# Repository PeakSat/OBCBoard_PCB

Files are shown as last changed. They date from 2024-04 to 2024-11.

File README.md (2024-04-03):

# AcubeSat - On Board Computer PCB

This repository contains schematics and layout files for
the On-Board Computer's PCB.

**NOTE:** EVERYTHING CONTAINED HERE IS UNTESTED AND WORK-IN-PROGRESS.
USE AT YOUR OWN RISK!

# Requirements
You will need **KiCad version 6** to open the schematics.
Your KiCad installation should contain the standard footprint library
in order for the layout files to be displayed normally.

# Usage
Open the `.kicad_pro` file in KiCad and then:
* choose the `.kicad_sch` file to view the schematic
* choose the `.kicad_pcb` file to view the PCB's layout.

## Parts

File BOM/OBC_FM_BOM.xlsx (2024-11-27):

Id | Designator | Footprint | Quantity | Designation | Supplier and ref | Tolerance | Min Op Temp | Max Op Temp | PPM/C | Power Rating
1 | CMD_EN,RTCI,WEN,TP27,ADDR_EN,TP32,TP31,TP45,TP10,NWP,PWM,BUSY,TP33,NOUT,TP37,TP34,TP47,NRST,TP49,TP36,GND,TP26,TP29,TP44,EN,TP6,RTCO,TP35,TP52,TP30,PWM,TP56,TP55 | TestPoint_Pad_D1.0mm | 33 | TestPoint_Small | - | - | - | - | -
2 | TP22,TP12,TP3,TP53,TP54 | TestPoint_Pad_D1.0mm | 5 | 5015 | - | - | - | - | -
3 | FID6,FID5,FID4,FID2,FID3,FID1 | Fiducial_0.5mm_Mask1mm | 6 | Fiducial | - | - | - | - | -
4 | 3V3_PROT,J29,ADCS_VDD,ADCS_VDDIO | PinHeader_1x01_P1.00mm_Vertical | 4 | Conn_01x01_Pin | - | - | - | - | -
5 | H4,H1,H3,H2 | MountingHole_3.2mm_M3_DIN965_Pad | 4 | MountingHole_Pad | - | - | - | - | -
 | D1 | FHA1105P-TR (LED_0402) | 1 | FHA1105P-TR | https://eu.mouser.com/ProductDetail/Stanley-Electric/FHA1105P-TR?qs=byeeYqUIh0MAYVMdncV%252BvA%3D%3D
6 | R65 | R_0603_1608Metric | 1 | 300k | https://gr.mouser.com/ProductDetail/Panasonic/ERJ-3EKF3003V | 1% | -55 | 155 | 100 | 100mW
7 | R90,R102,R101,R56,R99,R52,R64,R91,R58,R62,R89,R100,R104,R60,R54,R92,R50,R98,R97,R103 | R_0603_1608Metric | 20 | 1k | https://gr.mouser.com/ProductDetail/Panasonic/ERJ-3RBD102V?qs=FhbYA5MVMOXq%2Fpwdysel%252Bw%3D%3D | 0.5% | -55 | 155 | 50 | 100mW
8 | R83,R79,R77,R74 | R_0603_1608Metric | 4 | 30K | https://gr.mouser.com/ProductDetail/Panasonic/ERJ-S03F3002V?qs=Zyl8A9hlmJqIHk%2F7tV8Mgw%3D%3D | 1% | -55 | 155 | 100 | 100mW
9 | R117,R119,R118,R120 | R_0603_1608Metric | 4 | 0.5 | https://gr.mouser.com/ProductDetail/Wurth-Elektronik/560050316011?qs=unwgFEO1A6vnuH3MgbtkpQ%3D%3D
10 | R37,R126,R38,R127,R12,R23,R26,R11 | R_0402_1005Metric | 8 | 100k | https://gr.mouser.com/ProductDetail/Panasonic/ERJ-2RKF1003X?qs=H7k1u0Mp9JQnXoBKdf15Qg%3D%3D | 1% | -55 | 155 | 100 | 100mW
 | R19 | R_0402_1005Metric | 1 | 330 | https://eu.mouser.com/ProductDetail/Panasonic/ERA-2ARB331X?qs=6%252Bc%252B2ke79U7iqIhHbNRZlw%3D%3D
11 | R130,R48,R47,R131,R14,R15 | R_0402_1005Metric | 10 | 1.5k | https://gr.mouser.com/ProductDetail/Wurth-Elektronik/560112110095?qs=mELouGlnn3cs5mmpxmgsuw%3D%3D | 1% | -55 | 155 | 100 | 100mW
 | R9, R10, R20, R24 | R_0402_1005Metric | DNP | DNP
12 | R78,R73,R95,R93,R96,R76,R82,R94 | R_0603_1608Metric | 8 | 1K | https://gr.mouser.com/ProductDetail/Panasonic/ERJ-3RBD102V?qs=FhbYA5MVMOXq%2Fpwdysel%252Bw%3D%3D | 0.5% | -55 | 155 | 50 | 100mW
13 | R59,R55,R63,R61,R53,R51,R49,R57 | R_0603_1608Metric | 8 | 20k | https://gr.mouser.com/ProductDetail/Vishay-Beyschlag/MCT06030E2002BP500 | 0.1% | -55 | 125 | 15 | 100mW
14 | R18,R13 | R_0402_1005Metric | 2 | 120 | https://gr.mouser.com/ProductDetail/Panasonic/ERA-2AEB121X?qs=YFwoyZoVY0gzxkdhxiGxFA%3D%3D | 0.1% | -55 | 155 | 25 | 62.5mW
15 | R3,R6,R2,R1,R4,R5 | R_0603_1608Metric | 6 | 10k | https://gr.mouser.com/ProductDetail/Vishay-Dale/TNPW060310K0BEEA?qs=80vFmtL7BC940KIiWqacAA%3D%3D | 0.1% | -55 | 155 | 25 | 125mW
16 | R72,R71,R70 | R_0603_1608Metric | 3 | 500K | https://gr.mouser.com/ProductDetail/TE-Connectivity-Holsworthy/RN73C1J499KBTD | 0.1% | -55 | 155 | 10 | 62.5mW | Koutsou's Mailchain
17 | R67,R68,R66 | R_0603_1608Metric | 3 | 500k | https://gr.mouser.com/ProductDetail/TE-Connectivity-Holsworthy/RN73C1J499KBTD | 0.1% | -55 | 155 | 10 | 62.5mW | Koutsou's Mailchain
18 | R75,R81,R80,R85,R84,R86,R88,R87 | R_0603_1608Metric | 8 | 10K | https://gr.mouser.com/ProductDetail/Vishay-Dale/TNPW060310K0BEEA?qs=80vFmtL7BC940KIiWqacAA%3D%3D | 0.1% | -55 | 155 | 25 | 125mW
19 | R40,R28 | R_0603_1608Metric | 2 | 1.5M | https://gr.mouser.com/ProductDetail/Vishay-Beyschlag/MCT0603MD1504BP500?qs=Jslch3jnSjlJdBFlPxisJQ%3D%3D | 0.1% | -55 | 175 | 25 | 210mW
20 | R129,R128 | R_0603_1608Metric_Pad0.98x0.95mm_HandSolder | 2 | 100k | https://gr.mouser.com/ProductDetail/Panasonic/ERA-3AED104V?qs=MNPzkKEzRtQIWcmUWL4kjg%3D%3D | 0.5% | -55 | 155 | 25 | 100mW
21 | R124,R125,R123,R122 | R_0402_1005Metric | 4 | 100K | https://gr.mouser.com/ProductDetail/Panasonic/ERJ-2RKF1003X?qs=H7k1u0Mp9JQnXoBKdf15Qg%3D%3D | 1% | -55 | 155 | 100 | 100mW
22 | R42,R30 | R_0603_1608Metric | 2 | 1M | https://gr.mouser.com/ProductDetail/Vishay-Beyschlag/MCT0603MD1004BP500?qs=Jslch3jnSjlxqHB2XifrNA%3D%3D | 0.1% | -55 | 175 | 25 | 210mW
23 | R44,R32 | R_0603_1608Metric | 2 | 71.5k | https://gr.mouser.com/ProductDetail/Vishay-Dale/TNPW060371K5BEEA?qs=PRQR5v7TyD2hWSHu2r8kdg%3D%3D | 0.1% | -55 | 155 | 25 | 125mW
24 | R41,R29 | R_0603_1608Metric | 2 | 15k | https://gr.mouser.com/ProductDetail/Vishay-Dale/TNPW060315K0BEEA?qs=UyvxJcuXVAZVtbORYetIow%3D%3D | 0.1% | -55 | 155 | 25 | 125mW
25 | R43,R31 | R_0603_1608Metric | 2 | 402k | https://gr.mouser.com/ProductDetail/TE-Connectivity-Holsworthy/CPF0603B402KE1?qs=9ylKvqdyudlhpNaoEbd8Uw%3D%3D | 0.1% | -55 | 155 | 25 | 62.5mW
26 | R45,R33 | R_0603_1608Metric | 2 | 11.5k | https://gr.mouser.com/ProductDetail/Vishay-Dale/TNPW060311K5BEEA?qs=80vFmtL7BC9fSEwVMGaZLw%3D%3D | 0.1% | -55 | 155 | 25 | 125mW
27 | R69 | R_0603_1608Metric | 1 | 300K | https://gr.mouser.com/ProductDetail/Panasonic/ERJ-3EKF3003V | 1% | -55 | 155 | 100 | 100mW
28 | R8,R16,R17 | R_0603_1608Metric | 3 | DNP | - | - | - | - | - | -
29 | R7 | R_0603_1608Metric | 1 | 120? | https://gr.mouser.com/ProductDetail/Vishay-Dale/TNPW0603120RBEEA?qs=80vFmtL7BC8FomSVCn9jHA%3D%3D | 0.1% | -55 | 155 | 25 | 125mW
30 | R46,R34 | R_0603_1608Metric | 2 | 510k | https://gr.mouser.com/ProductDetail/TE-Connectivity-Holsworthy/CPF0603B510KE?qs=gt1LBUVyoHkDJXf78dveiw%3D%3D | 0.1% | -55 | 155 | 25 | 62.5mW
31 | C45,C59,C64,C60,C57,C62,C58,C55,C52,C54,C50,C66,C61,C46,C2,C48,C93,C51,C53,C65,C1,C63,C47,C35,C19,C33,C40,C20,C26,C18,C41,C91,C28,C23,C31,C37,C22,C32,C39,C42,C34,C36,C29,C17 | C_0402_1005Metric | 44 | 100n | https://gr.mouser.com/ProductDetail/KYOCERA-AVX/0402X7R104KT7AT | 10% | -55 | 125
32 | C100,C98,C97,C102,C101,C99 | C_0603_1608Metric | 6 | 1n | https://gr.mouser.com/ProductDetail/KYOCERA-AVX/KAM15AR72A102KT?qs=Jm2GQyTW%2Fbi5i5WV3n7jRg%3D%3D | 10% | -55 | 125
33 | C67,C70,C69,C68 | C_0603_1608Metric | 4 | 0.1u | https://gr.mouser.com/ProductDetail/KEMET/C0603C104K1RACAUTO?qs=3Rah4i%252BhyCGTQ5uPNXtfZA%3D%3D | 10% | -55 | 125
34 | C71,C72,C77,C75,C78,C76,C74,C73 | C_0603_1608Metric | 8 | 4.7u | https://gr.mouser.com/ProductDetail/Samsung-Electro-Mechanics/CL10Y475KQ96PNC?qs=Imq1NPwxi76jTVrSUIqrWA%3D%3D | 10% | -55 | 125 | Koutsou's Mailchain
35 | C43,C44,C21,C24 | C_0603_1608Metric | 4 | 11p | https://gr.mouser.com/ProductDetail/KEMET/CBR06C110J5GACAUTO?qs=By6Nw2ByBD3H%252Bc1ndrodgw%3D%3D | 5% | -55 | 125
36 | C27,C25 | C_0603_1608Metric | 2 | 100n | https://gr.mouser.com/ProductDetail/KEMET/C0603C104K1RACAUTO?qs=3Rah4i%252BhyCGTQ5uPNXtfZA%3D%3D | 10% | -55 | 125
37 | C95,C96,C92,C94 | C_0603_1608Metric | 4 | 10u | https://gr.mouser.com/ProductDetail/TAIYO-YUDEN/MSASL168BB5106KTNB33?qs=tlsG%2FOw5FFgv8vGbRXU%2FLg%3D%3D | 10% | -55 | 125
38 | C56,C38 | C_0603_1608Metric | 2 | 1u | https://gr.mouser.com/ProductDetail/Samsung-Electro-Mechanics/CL10B105KB9VPNC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 | 10% | -55 | 125
39 | C49,C30 | C_0603_1608Metric | 2 | 4.7u | https://gr.mouser.com/ProductDetail/Samsung-Electro-Mechanics/CL10Y475KQ96PNC?qs=Imq1NPwxi76jTVrSUIqrWA%3D%3D | 10% | -55 | 125
40 | U7 | MR4A08BUYS45 | 1 | MR4A08BUYS45 | https://gr.mouser.com/ProductDetail/Everspin-Technologies/MR4A08BUYS45?qs=BZBei1rCqCDatmS%252BkCPglA%3D%3D | Sourced from old BOM
41 | U18,U17,U11,U10 | TCAN337GDR | 4 | TCAN337GD | https://gr.mouser.com/ProductDetail/?qs=gMfM3zrbS4qJ%252BEWbPaeUtA%3D%3D | Sourced from old BOM
42 | U16,U14 | For EM: ATSAMV71Q21B-AAB (procured by Prisma) For FM: SAMV71Q21RT-H8X-HP (to be sent by AUTh) | 2 | ATSAMV71Q21B-AAB | https://gr.mouser.com/ProductDetail/Microchip-Technology/ATSAMV71Q21B-AAB?qs=j%252B1pi9TdxUaaYXmCSj2x3Q%3D%3D | Sourced from old BOM | Comment: As discussed first the top-side component will be assembled (U16). Then PeakSat team to perform a functional test at Prisma facilities. Afterwards, the bottom side will be assembled
43 | U19,U20,U13,U12 | MCP9808T-E_MS | 4 | MCP9808T-E_MS | https://gr.mouser.com/ProductDetail/Microchip-Technology/MCP9808T-E-MS?qs=sGAEpiMZZMtEh3uSYjX9TlCqmnCacfrl | Sourced from old BOM
44 | U8,U15 | LTC4367 | 2 | LTC4367 | https://gr.mouser.com/ProductDetail/Analog-Devices/LTC4367IMS8PBF?qs=oahfZPh6IAL2dJuXCqiwOw%3D%3D | Sourced from old BOM
45 | Q8,Q10,Q7,Q9 | PMV28XPEAR | 4 | PMV28XPEAR | https://www.mouser.co.uk/ProductDetail/Nexperia/PMV28XPEAR?qs=W%2FMpXkg%252BdQ6VcRCVGMTksA%3D%3D | Sourced from old BOM
46 | Q6,Q5,Q3,Q4 | 2N7002NXAKR | 4 | 2N7002NXAKR | https://gr.mouser.com/ProductDetail/Nexperia/2N7002NXAKR?qs=%252B6g0mu59x7JoAsZYPFXqhw%3D%3D | Sourced from old BOM
47 | Q1,Q2 | SI6926ADQ-T1-E3 | 2 | SI6926ADQ-T1-E3 | https://gr.mouser.com/ProductDetail/Vishay-Semiconductors/SI6926ADQ-T1-E3?qs=jcx%252B0HVgj2aS1Th5vt1wDw%3D%3D | Sourced from old BOM
48 | Y3,Y2 | ECSTXO252033120ANTR | 2 | ECS-TXO-2520-33-120-AN-TR | https://gr.mouser.com/ProductDetail/ECS/ECS-TXO-2520-33-120-AN-TR?qs=KAq9QXcE8HB8zqkkQbQ2Dw%3D%3D | Sourced from old BOM
49 | Y4,Y1 | FC135327680KAAG3 | 2 | FC-135_32.7680KA-AG3 | https://gr.mouser.com/ProductDetail/Epson-Timing/FC-135-327680KA-AG3?qs=l3LL3yk8ONbdhVAPUR8zug%3D%3D | Sourced from schematic
50 | IC2,IC4,IC3,IC5 | TLC555QDR | 4 | TLC555QDR | https://gr.mouser.com/ProductDetail/Texas-Instruments/TLC555QDRQ1?qs=t6sYTo5dwUycH9kiYHOzsw%3D%3D | Sourced from old BOM
51 | IC6 | TVL2254AIDR | 1 | TLV2254AIDR | https://gr.mouser.com/ProductDetail/Texas-Instruments/TLV2254AIDR?qs=Fg5TsMy7H4tEDlpHSjkW%252BQ%3D%3D | Sourced from old BOM
52 | IC1 | SOP50P2000X120-48N | 1 | MT29F64G08AFAAAWP-ITZ_A_TR | https://gr.mouser.com/ProductDetail/Micron/MT29F64G08AFAAAWP-ITZA-TR?qs=taEdVNyAfdHwqoLheszjbg%3D%3D | Sourced from old BOM
53 | IC8,IC9 | SOIC127P600X175-14N | 2 | ADM3491ARZ-REEL7 | https://gr.mouser.com/ProductDetail/Analog-Devices/ADM3491ARZ-REEL7?qs=BpaRKvA4VqFzaBp8iOiNPQ%3D%3D | Sourced from old BOM
54 | F11,F12 | MF-ASML035_6-2 | 2 | MF-ASML035_6-2 | https://gr.mouser.com/ProductDetail/Bourns/MF-ASML035-6-2?qs=mAH9sUMRCtug7KIM9%2Fa3qA%3D%3D | Sourced from schematic
55 | F13,F14 | FEMTOASMDC005F-2 | 2 | FEMTOASMDC005F-2 | https://gr.mouser.com/ProductDetail/Littelfuse/FEMTOASMDC005F-2?qs=l5LPopohbqT5KxfEbLNj7A%3D%3D | Sourced from schematic
56 | FL6,FL4,FL5,FL3,FL1,FL2 | BLM18PG471SH1D | 6 | 470 @ 100 MHz | https://gr.mouser.com/ProductDetail/Murata-Electronics/BLM18AG471WH1D?qs=%2F%252BYoplLUB5hrHFZEz1jXRg%3D%3D | Sourced from schematic
57 | F5,F10 | MFPSML075122 | 2 | MF-PSML075_12-2 | https://gr.mouser.com/ProductDetail/Bourns/MF-PSML075-12-2?qs=T3oQrply3y8tiS9BILrBxw%3D%3D | Sourced from schematic
58 | F8,F9 | FUSC1607X85N | 2 | 0ZCM0001FF2G | https://gr.mouser.com/ProductDetail/Bel-Fuse/0ZCM0001FF2G?qs=uwxL4vQweFOSr3rpPGffpA%3D%3D | Sourced from schematic
59 | F7,F6 | FUSC1608X85N | 2 | FEMTOSMDC016F-2 | https://gr.mouser.com/ProductDetail/Littelfuse/FEMTOSMDC016F-2?qs=5HUSoMAf2%252BoNWb7nt5%252BK9w%3D%3D | Sourced from schematic
60 | J6,J3,J4,J2 | DF584P12V21 | 4 | DF58-4P-1.2V_21_ | https://www.mouser.co.uk/ProductDetail/Hirose-Connector/DF58-4P-12V21?qs=7bTaA%2FLYtSZD8VmLOAYe3A%3D%3D | Sourced from schematic
61 | J15,J18 | SSM104LSVTR | 2 | SSM-104-L-SV-TR | https://www.mouser.co.uk/ProductDetail/Samtec/SSM-104-L-SV-TR?qs=rU5fayqh%252BE12yhO8FhHaEQ%3D%3D | Sourced from schematic
62 | J10,J11,J14,J9 | 5040500491 | 4 | 504050-0491 | https://www.mouser.co.uk/ProductDetail/Molex/504050-0491?qs=yXHQdf%252Bjwlut3yyE1%252ByhMA%3D%3D | Sourced from schematic
63 | J16,J20 | 5037630691 | 2 | 503763-0691 | https://gr.mouser.com/ProductDetail/Molex/503763-0691?qs=d9U39LAeJF2PVpSXMliCdg%3D%3D | Sourced from schematic
64 | J17 | M80-66626YY | 1 | M80-6662622 | https://gr.mouser.com/ProductDetail/Harwin/M80-6662622?qs=IQR8xM2KsGhXAWHQWi6yag%3D%3D | Sourced from schematic
65 | J1,J5 | SAMTEC_ESQ-126-14-G-D-LL | 2 | ESQ-126-14-G-D-LL | https://hr.mouser.com/ProductDetail/Samtec/ESQ-126-14-G-D-LL?qs=3%252BjIH0OdpA%252BquPqGEkv%252Bag%3D%3D
66 | J7 | M80-66610YY | 1 | M80-6661022 | https://gr.mouser.com/ProductDetail/Harwin/M80-6661022?qs=IQR8xM2KsGgh%252BokSH0w3Qw%3D%3D | Sourced from schematic
67 | J12 | M808420642 | 1 | M80-8420642 | https://gr.mouser.com/ProductDetail/Harwin/M80-8420642?qs=7jyBjEprRBgCB95Y5ZrUpQ%3D%3D | Sourced from schematic
68 | J24 | FTS10201LSV | 1 | DNP | - | - | - | -

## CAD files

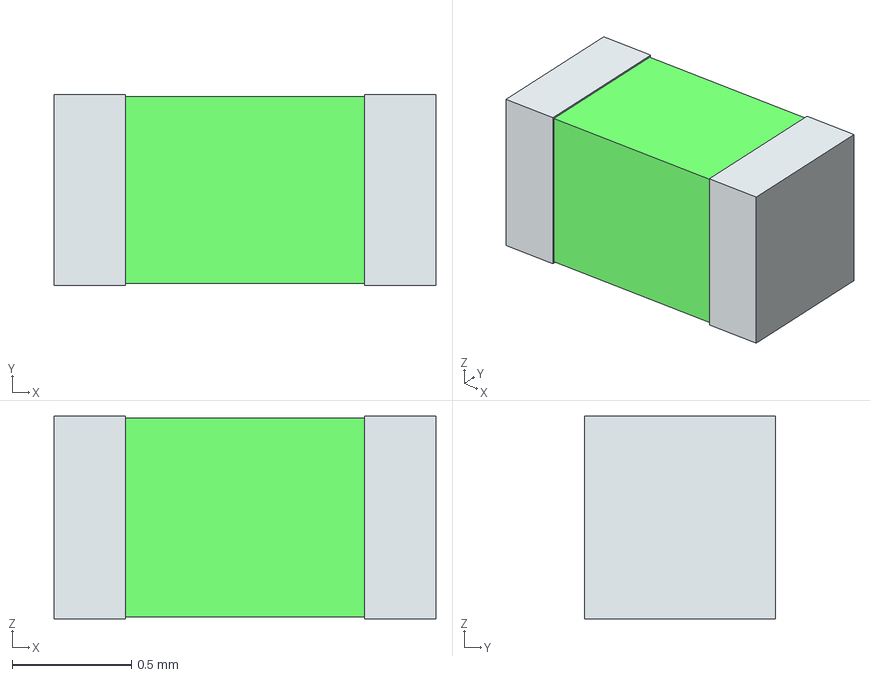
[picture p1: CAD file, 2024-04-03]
3D/step/FEMTOASMDC005F-2.stp
1.60 x 0.8 x 0.85 mm
term1
term2

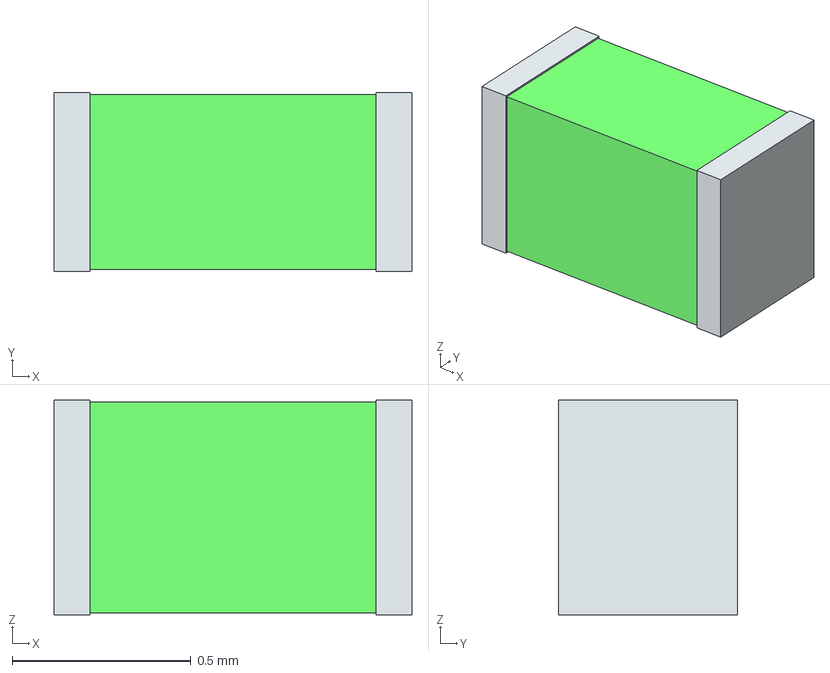
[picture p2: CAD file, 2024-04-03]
3D/step/MF-ASML035_6-2.stp
1.00 x 0.5 x 0.6 mm
term1
term2

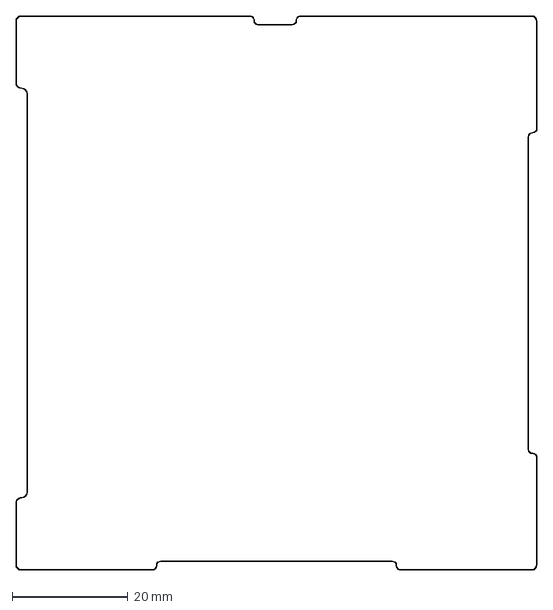
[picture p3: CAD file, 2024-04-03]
3D/DXF/obs-adcs-dxf1.dxf
90.2 x 95.9 mm

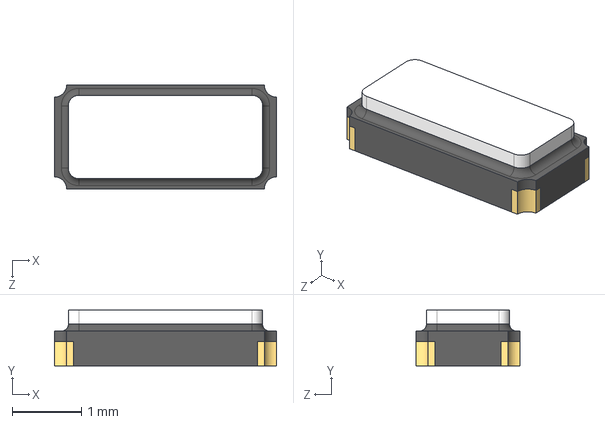
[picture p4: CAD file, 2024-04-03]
3D/step/FC-135_32.7680KA-AG3.stp
3.20 x 0.8 x 1.50 mm

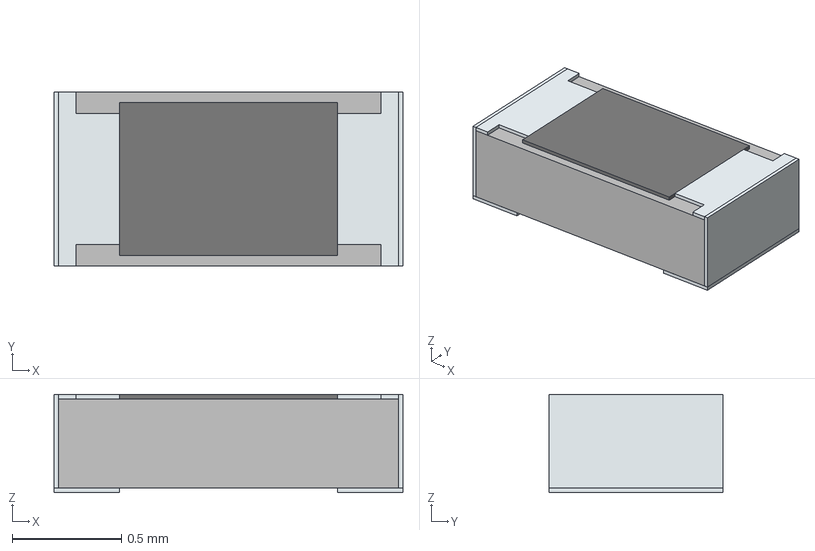
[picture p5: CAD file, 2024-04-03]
3D/step/ERA-3AED3921V.stp
1.60 x 0.8 x 0.45 mm
solidBody
solidTop
solidTerminal1
solidTerminal2
solidTerminal3

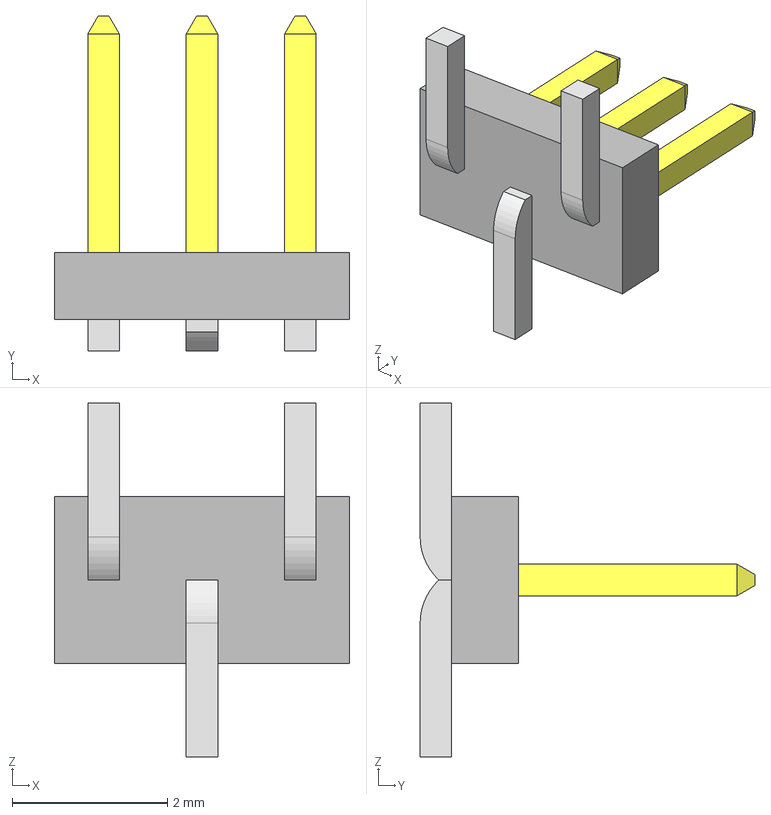
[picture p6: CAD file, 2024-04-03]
3D/step/FTS-103-01-L-SV.stp
3.81 x 4.32 x 4.57 mm
FTS-103-01-L-SV_pins2
FTS-103-01-L-SV_pins1
FTS-103-01-L-SV_body

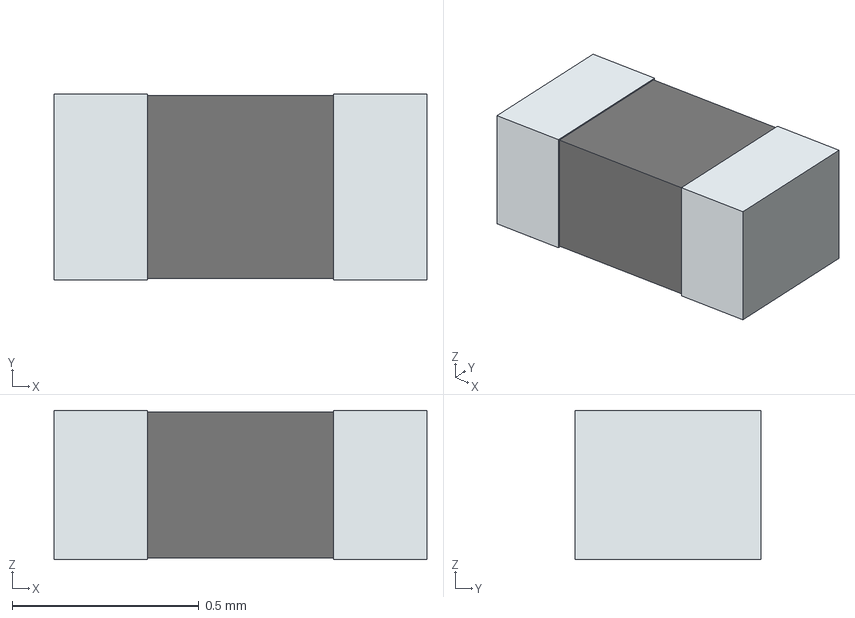
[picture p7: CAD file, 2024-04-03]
3D/step/ERJ-2RHD203X.stp
1.00 x 0.5 x 0.4 mm
term1
term2

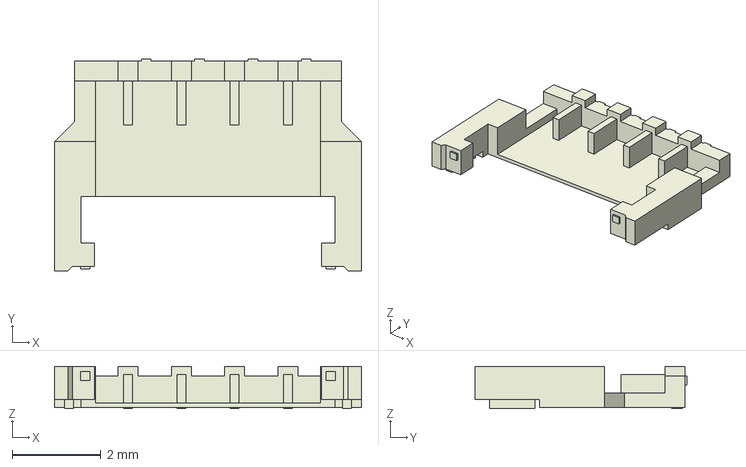
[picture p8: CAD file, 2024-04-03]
3D/step/DF58-4P-1.2V.stp
6.90 x 4.77 x 0.95 mm

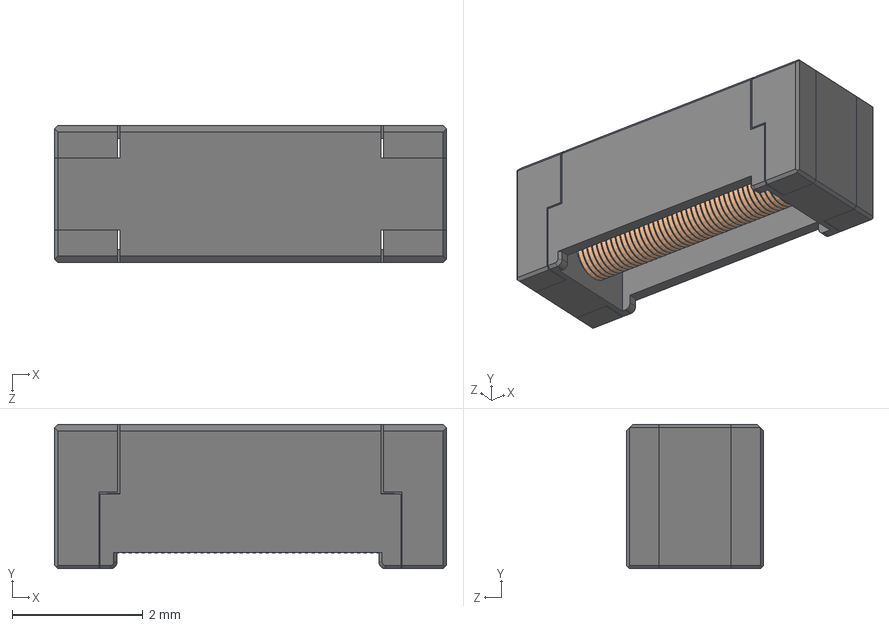
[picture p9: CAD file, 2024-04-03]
3D/step/RM-3100 Sen-XY-f.STEP
6.00 x 2.21 x 2.10 mm

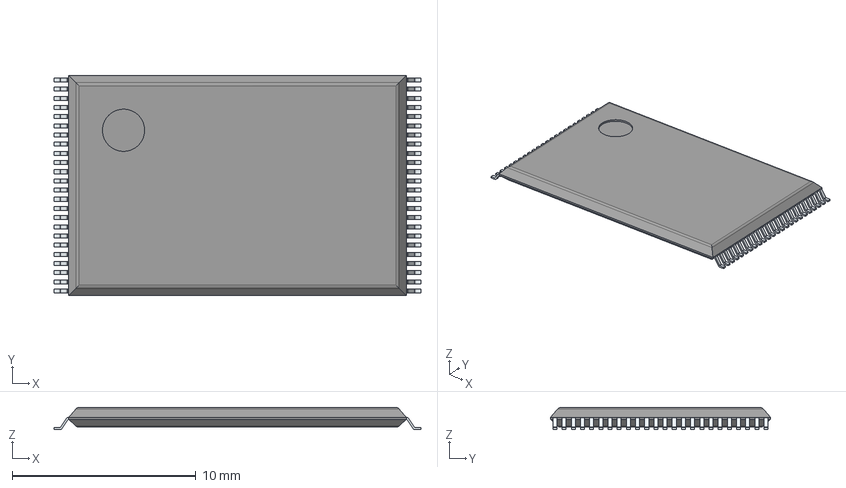
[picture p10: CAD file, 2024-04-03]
3D/step/MT29F32G08ABAAAWP-ITZ_A.stp
20.0 x 12.0 x 1.20 mm
PinsArrayLR

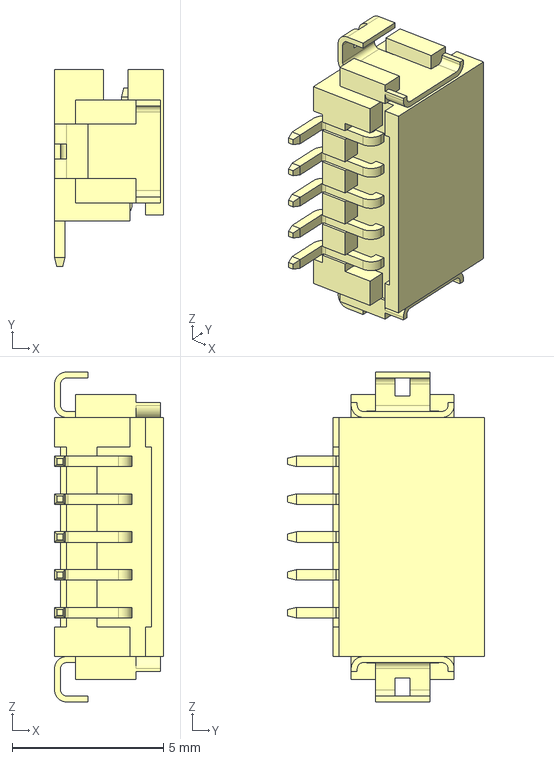
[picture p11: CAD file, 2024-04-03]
3D/step/DF13A-5P-1.25H.stp
3.60 x 6.50 x 10.9 mm

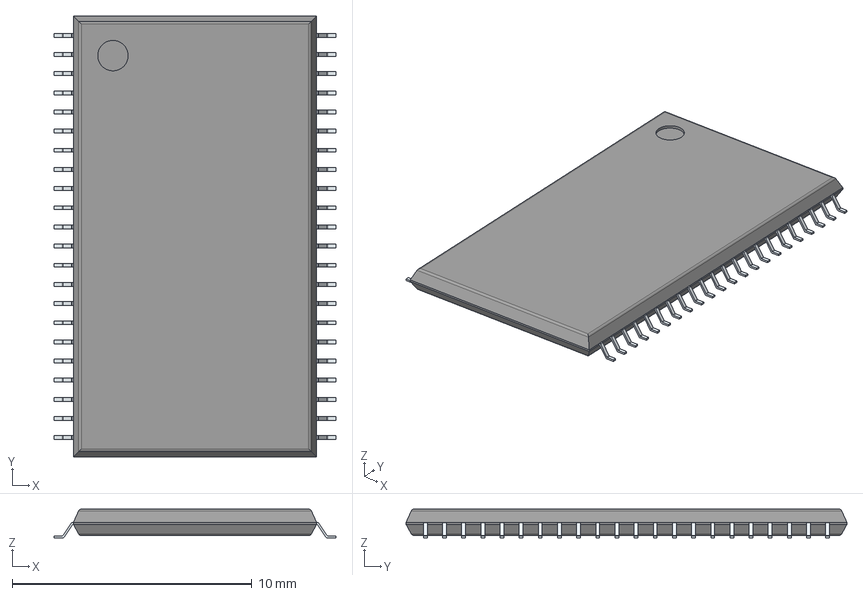
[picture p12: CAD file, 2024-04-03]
3D/step/MR4A08BUYS45.stp
11.8 x 18.4 x 1.20 mm
PinsArrayLR

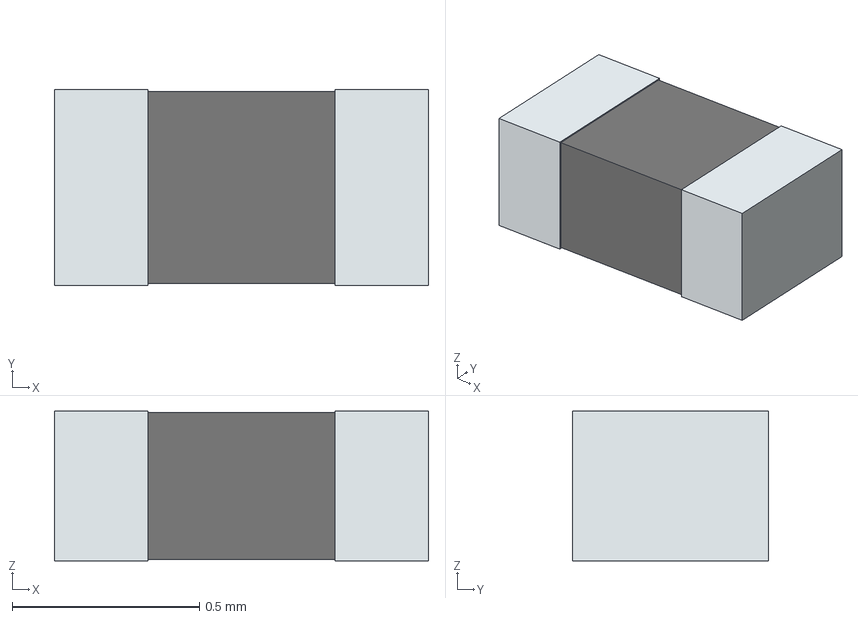
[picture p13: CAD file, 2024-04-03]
3D/step/ERA-2VEB1501X.stp
1.00 x 0.525 x 0.4 mm
term1
term2

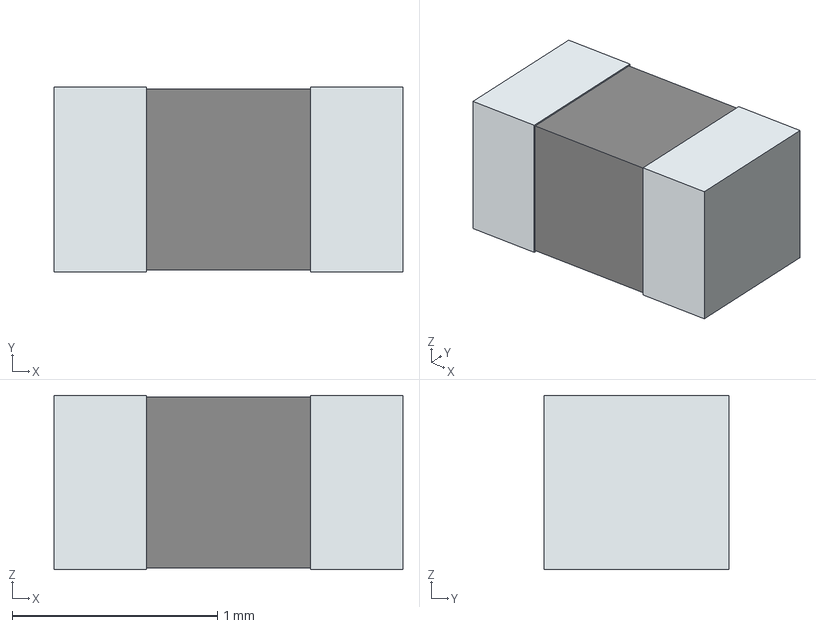
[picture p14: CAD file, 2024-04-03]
3D/step/TS4448_RGG.stp
1.70 x 0.9 x 0.85 mm
term1
term2

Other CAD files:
3D/step/SFR01MZPF1504.stp
3D/step/ERA-2AEB303X.stp
3D/step/ERA-2AED104X.stp
3D/step/ERJ-2RKF3003X.stp
3D/step/2035590607.stp
3D/step/205972-0021.stp
3D/step/205972-0081.stp
3D/step/2N7002NXAKR.stp
3D/step/5015--3DModel-STEP-1.STEP
3D/step/504050-0491.stp
3D/step/78171-0002.stp
3D/step/ADXRS453BRGZ.stp
3D/step/BLM18PG471SH1D.stp
3D/step/C0603C162JAGACTU.stp
3D/step/DF57H-3P-1.2V.stp
3D/step/DF58-6P-1.2V.stp
3D/step/ECS-TXO-2520-33-160-AN-TR.STEP
3D/step/ERA-2AEB623X.stp
3D/step/ERA-2ARB331X.stp
3D/step/ERA-2ARB511X.stp
3D/step/ERA-2VEB1002X.stp
3D/step/ERA-2VEB1200X.stp
3D/step/ERJ-2RKD105X.stp
3D/step/ESQ-126-39-G-D.stp
3D/step/FBMH2016HM251NT.stp
3D/step/FTS-102-01-L-SV.stp
3D/step/GCM155R71H104KE02J.stp
3D/step/GCQ1555C1H110JB01D.stp
3D/step/GRT155R61A475ME13D.stp
3D/step/GRT155R61E105KE01D.stp
3D/step/LCC_V (EY-14-1).STEP
3D/step/LTC4367IMS8#PBF.stp
3D/step/M80-6661022.stp
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

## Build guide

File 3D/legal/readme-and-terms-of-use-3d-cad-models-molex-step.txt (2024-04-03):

EN   Your download at 01/08/2021 on PARTcommunity/PARTserver:

       Dear user,
       
       attached please find the following file of our 3D CAD download portal PARTcommunity/PARTserver powered by CADENAS:

       STEP, 2035590607, 2035590607.stp
	
       Information for use:

       The attached file was compressed ("ZIP"), in order to ensure a faster download.
       In order to unpack the file you need a special decompressing software. 

       If you do not have a decompressing software installed, you can download it using one of the following links:
       PKZip® (http://www.pkware.com) or WinZip® (http://www.winzip.com)

       Please also check terms of use at http://www.cadenas.de/terms-of-use-3d-cad-models

       Best regards

       Your CADENAS GmbH
       support@cadenas.de

       >> Free APP for 3D CAD models <<
       
       Mobile access to 3D CAD models with your Smartphone or Tablet PC. 
       
       Download now at http://www.cadenas.de/en/app-store

       >> PARTcommunity - The network and information platform for engineers <<
       
       ■ Examples of use and ideas for components 
       ■ Information and experience exchange with other engineers

       Join the discussion now at http://www.partcommunity.com

       >> PARTsolutions - Find & manage standard, purchased, and own parts <<

       Reduce total product costs up to 70% in the development phase?

       In many companies PARTsolutions is one of the leading software systems helping
       engineers and purchasers to manage and find company-, supplier- and standard parts:

       ■ PURCHINEERING: Optimize cooperation of Purchasing and Engineering
       ■ Semiautomatic classification and intelligent search methods
       ■ Open for all systems such as PLM and ERP

       More information at http://www.cadenas.de/strategic-partsmanagement

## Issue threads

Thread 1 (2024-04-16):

J19 and J17 Umbilical Connectors

Basilhs-Moustakas, 2024-04-16:
We need to remove J19 connector and instead make J17 26 pin with the following pinout:

 Pinout for J17 ([M80-6662622](https://gr.mouser.com/ProductDetail/Harwin/M80-6662622?qs=IQR8xM2KsGhXAWHQWi6yag%3D%3D)):

+ OBC SWDIO
+ OBC SWCLK
+ ADCS_UART_TX
+ ADCS_UART_RX
+ CAN1+
+ CAN1-
+ OBC RST
+ OBC 3V3 REF
+ GND
+ ADCS SWDIO
+ ADCS SWCLK
+ OBC_UART_RX
+ OBC_UART_TX
+ CAN2+
+ CAN2-
+ ADCS_RESET
+ GND
+ COMMS VREF 3V3
+ COMMS SWDIO
+ COMMS SWCLK
+ COMMS RESET
+ COMMS UART RX
+ COMMS UART TX

The COMMS signals also need to be added on the PC104

giatats, 2024-04-16:
Done

Basilhs-Moustakas, 2024-04-17:
OK but you should now remove the J19 connector

Closed 2024-04-16.

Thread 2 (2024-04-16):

Payload Connector

Basilhs-Moustakas, 2024-04-16:
Power supply and CAN should be removed from Payload connector. Also we should add a direct connection with PPS

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

giatats, 2024-04-16:
Change tthe connector to 4-pin Molex?
RS422_A, RS422_B, GND, PPS

Basilhs-Moustakas, 2024-04-17:
Yes it will help save valuable space. We can do 6 pin if 2 differential pairs are needed.

Closed 2024-04-23.

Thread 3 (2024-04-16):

RS-422 interface

Basilhs-Moustakas, 2024-04-16:
I think RS-422 is a bit sus. For some reason the payload has 2 differential pairs for the RS-422 interface while the ADM3483 has indeed 2 connections for both input and output. Perhaps they are using the ADM3488 version and I was wrong? I think we need to clarify with them.

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

giatats, 2024-04-16:
Mail to Astrolight for clarification.

Basilhs-Moustakas, 2024-04-22:
@giatats I think we also need termination resistor somewhere. Typically the circuit looks like this which, however Astrolight specifies that they only place termination resistor on A-B end... I think we should do the same.

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

Basilhs-Moustakas, 2024-04-22:
ok so there is an RS-422 impementation guide from analog circuits. Here we can see this:

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

So from what I understand we need to place an 120Ohm termination resistor on our Z-Y end an then have a 60Ohm impedance cable to connect to the terminal

Closed 2024-04-23.

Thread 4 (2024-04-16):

Notes on ERC errors

Basilhs-Moustakas, 2024-04-16:
1. EPS_RX and EPS_TX will now be COMMS_RX and COMMS_TX and should be connected to J19 umbilical
2. ADCS_RW_3V3 can be completely removed
3. VDD_RW can be removed
4. VREF can be removed
5. VDD can be removed
6. USR_ADC_1,2 can be removed
7. MCU_VDDIO, MCU_VDDIN, MCU_VDDIO and the rest of the connections to test points were not supposed to give an error. Something is wrong here
8. EPS_3V3_SU and EPS_12V_SU can also be removed
9. PAY_SWITCH can be removed
10. SU_3V3 and SU_12V can be removed
11. 3V3_PROT on RS-422 OBC sheet is a problem that has to be fixed
12. SU_SWDIO can be removed
13. SU_SWCLK can be removed
14. 3V3_ADCS on RS-422 ADCS sheet is a problem

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

giatats, 2024-04-16:
Fixed many of them, some persist, maybe you can take a look, mainly for the 2 remaining errors.

giatats, 2024-04-16:
To EPS_5V_ADM ston 104 einai se 2 pin, na ta kanw short?

Basilhs-Moustakas, 2024-04-17:
For the EPS_5V_ADM yes

For the ERC errors somehow I still get 14 of them. I think that it is just kicad being stupid with the grid though. Can you show me the errors you get?

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

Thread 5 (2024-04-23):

GND Vias Placement

Basilhs-Moustakas, 2024-04-23:
The power plane in this area is almost cut in half by these four vias. Furthermore one of the vias are placed almost on top of the pad which can lead to assembly issues. Is it possible to fine tune their position?

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

giatats, 2024-04-24:
moved vias around

Closed 2024-04-24.

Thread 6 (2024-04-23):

RS-422 charachteristic impedance

Basilhs-Moustakas, 2024-04-23:
Since we are going with 120 Ohm charachteristic impedance on both ends we should have a controlled impedance between RS-422 A-B and RS-422 Y-Z. We shall use the "Route differential tool" of Kicad for this. The width and min clearance in the differential pair is also important when routing and are different for each layer, depending on the GND layers distance from it. You can check in each layer the parameters with which the AcubeSAT guys have routed CAN bus and apply the same since they also went for 120 Ohm differential impedance.

Alternatively you can also use the Kicad calculator tool. Dont take too much time trying to find the exact number for which you get 120Ohm.

Also the traces of each differential pair should be, ideally, the same length.  There is a tool for fine tuning track lengths by Kicad in the "Route" dropdown menu.

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

Basilhs-Moustakas, 2024-04-24:
Length tuning is fine but you also need to route them as differantial pairs for the channel to have a proper characteristic impedance

Closed 2024-04-25.

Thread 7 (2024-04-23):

CAN differential pair

Basilhs-Moustakas, 2024-04-23:
For a small part of the track length there is no impedance control for both CAN bus channels. I mean in nominal conditions this might not be a problem but with the long TVAC cables and extreme temperature you dont want to risk it. Match the tracks length as well.

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

Basilhs-Moustakas, 2024-04-24:
Length tuning is fine but you also need to route them as differantial pairs for the channel to have a proper characteristic impedance

giatats, 2024-04-24:
Done

Closed 2024-04-24.

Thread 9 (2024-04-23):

ADM 5V

Basilhs-Moustakas, 2024-04-23:
We expect up to 2A in the EPS_5V_ADM track. 0.3mm is definetely not sufficient. Try to have a dedicated power filled zone in a different layer or make it at least 1.5mm wide. Use the track width calculator tool to measure voltage drop. Anything above 0.05V should not be acceptable.

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

Basilhs-Moustakas, 2024-04-23:
GND shall also have a thick track and probably multiple vias as well. For the number of vias needed you can also use the calculator tool of kicad

Basilhs-Moustakas, 2024-04-24:
Cool but whats stopping us from making it bigger like this? Also why this no copper zone on the left?

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

giatats, 2024-04-24:
Re-arranged power planes

Closed 2024-04-24.

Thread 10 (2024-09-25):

[FM] Final interface changes

maestroque, 2024-09-25:
- [x] PC/104 Finalization
- [x] Umbilical Connector Update (Vbat routing)
- [x] Add ADCS Boot/Enable pins
- [x] Add User LED

maestroque, 2024-10-15:
@giatats take a look whenever you can.

If you have any other additions in mind let me know

Closed 2024-10-24.

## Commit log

2024-04-15 General Changes & Added RS422 module
    [RS422_Transceiver_main.kicad_sch, can-transceivers.kicad_sch, canbus.kicad_sch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]
2024-04-15 Finished RS422 schematic
    [RS422_Transceiver_red.kicad_sch, connectors.kicad_sch, main.kicad_sch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]
2024-04-16 Resolved issues
    [RS422_Transceiver_main.kicad_sch, RS422_Transceiver_red.kicad_sch, can-transceivers.kicad_sch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]
2024-04-22 Added ADM3491 & Updated schematic
    [RS422_Transceiver_main.kicad_sch, RS422_Transceiver_red.kicad_sch, connectors.kicad_sch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]
2024-04-22 Final schematic
    [RS422_Transceiver_main.kicad_sch, RS422_Transceiver_red.kicad_sch, can-transceivers.kicad_sch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]
2024-04-22 Finished layout
    [connectors.kicad_sch, test-points.kicad_sch]
2024-04-25 Added logo to silkscreen & moved red connector
2024-04-25 minor silkscreen updates
2024-04-25 Generate Gerbers & Route Differential pairs
    [obc-adcs-board-ADCS_Inner_signals_6_Cu.gbr, obc-adcs-board-B_ADCS_8_Cu.gbl, obc-adcs-board-B_ADCS_8_Cu.gbr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]
2024-04-30 Generate BOM
    [OBC_BOM.xlsx]
2024-10-14 PCB: Update PC/104
    [RS422_Transceiver_main.kicad_sch, RS422_Transceiver_red.kicad_sch, can-transceivers.kicad_sch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]
2024-10-15 Update system umbilical connector
    [connectors.kicad_sch]
2024-10-15 Add CubeADCS boot and enable pins and user LED
    [main.kicad_sch, mcu.kicad_sch, obc-adcs-board.kicad_sch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]
2024-10-21 Update PC/104
    [obc-adcs-board.kicad_sch]
2024-10-22 Add FM Gerbers
2024-10-24 PC104: Add redundant UHF Antenna channel
    [obc-adcs-board.kicad_sch]
2024-10-29 SCH: Update MCU TCXO to 12MHz on schematic
    [mcu.kicad_sch]
2024-10-29 SCH: Update OBC FM PC/104 connector PN
    [obc-adcs-board.kicad_sch]
2024-10-29 Update FM BOM
    [OBC_BOM.xlsx]
2024-11-11 Add updated step file
    [504050-0491.stp, M80-6662622.stp, M80-8420642.stp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]
2024-11-27 RED I2C pull-ups mark as DNP (BUS and UHF)
    [OBC_FM_BOM.xlsx, mcu.kicad_sch]
2025-05-13 Mark all RED circuitry as DNP
    [RS422_Transceiver_red.kicad_sch, canbus.kicad_sch, connectors.kicad_sch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]

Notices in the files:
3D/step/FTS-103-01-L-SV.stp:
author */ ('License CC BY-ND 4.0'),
